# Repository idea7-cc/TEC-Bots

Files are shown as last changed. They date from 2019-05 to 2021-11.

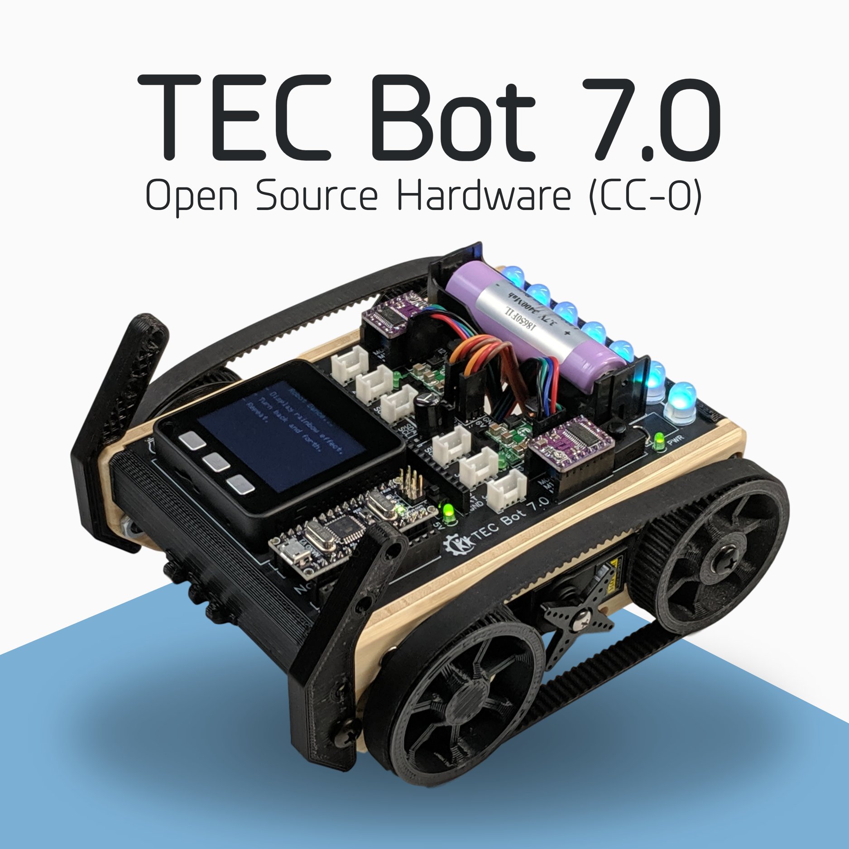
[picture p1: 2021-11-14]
TEC Bot 7/Tecbot7.jpg

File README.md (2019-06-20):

# Idea7 TEC Bots
This repo is for all of the TEC Bot series Idea7 Robots.  Robots prior to the creation of this repo may be added in time.  New TEC Bots and support files will be maintained here.

The TEC Bot series started as a spin-off of the series of robot kits that were being created by TEC Hub Foundation for Virginia Space Flight Academy's Advanced Robotics Camp.  When Cornell University added a new robotics course to their Summer College line-up, the TEC Bot series was a natural choice. 

## Robots for Cornell University's Summer College Program, "Fabricating the Future: Robotics and Programming."

- TEC Bot 3.5: 2016
- TEC Bot 4.2: 2017
- Bambot (TEC Bot 5.6): 2018
- TEC Bot 7: 2019

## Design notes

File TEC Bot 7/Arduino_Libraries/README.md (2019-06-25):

# Custom Arduino Libraries for the TEC Bot 7

- grbl4bots

# Libraries that can be found in the Arduino Library Manager

- M5Stack
- FastLED
- NewPing
- QTRSensors

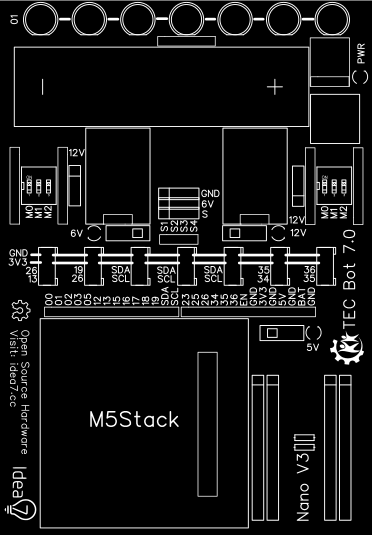
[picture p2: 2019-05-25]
TEC Bot 7/Base PCB/Top Silkscreen.png

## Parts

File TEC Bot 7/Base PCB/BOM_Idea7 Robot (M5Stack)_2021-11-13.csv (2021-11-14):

ID | Name | Designator | Footprint | Quantity | Manufacturer Part | Manufacturer | Supplier | Supplier Part | Price
1 | 1125S-4P | A1,A2,D1,D2,I2C1,I2C2,I2C3 | HW4-2.0 | 7 | 1125S-4P
2 | GPTS203211B Switch | B1 | GPTS203211B | 1 | ?
3 | BLOSSM 18650-PC2 | BAT1 | BLOSSM 18650-PC2 | 1 | BLOSSM 18650-PC2
4 | Header-Female-2.54_1x8 | DRV1,DRV2,DRV3,DRV4 | HDR-8X1/2.54 | 4 | Female headerHDR1X8-2.54 | BOOMELE | LCSC | C27438 | 0.073
5 | Header-Female-2.54_1x15 | H1,H2,H6,H7 | DIP-1X15P2.54 | 4 | 220S-1*15P H=8.5MM Ytype Gold-plated | Ckmtw | LCSC | C124408 | 0.176
6 | Header-Male-2.54_1x4 | H3,H4,H5,H8,H9 | DIP-1X4P-2.54MM-M | 5 | 210S-1*4P L=11.6MMGold-plated black | Ckmtw | LCSC | C124378 | 0.028
7 | WS2812D-F8 | LED1,LED2,LED3,LED8,LED9,LED10,LED11 | LED-8.0-RGB4P | 7 | WS2812D-F8 | Worldsemi | LCSC | C139126 | 0.161
8 | LED-3MM | LED4,LED5,LED6,LED7 | LED-3MM/2.54 | 4 | 204-10SURD/S530-A3 | EVERLIGHT | LCSC | C99772 | 0.038
9 | Header-Female-2.54_1x4 | P1,P5 | HDR-4X1/2.54 | 2 | Header-Female-2.54_1x4 | ReliaPro | LCSC | C124413 | 0.089
10 | Female header 2.54-1*14P | P2,P4 | HDR-14X1/2.54 | 2 | Female header 2.54-1*14P | BOOMELE | LCSC | C52711 | 0.075
11 | Header-Male-2.54_2x15 | P3 | HDR-15X2/2.54 | 1 | 2.54-2*15PDouble Rows | BOOMELE | LCSC | C56496 | 0.121
12 | Header-Male-2.54_1x6 | P6 | HDR-6X1/2.54 | 1 | Header-Male-2.54_1x6 | BOOMELE | LCSC | C37208 | 0.024
13 | Header-Female-2.54_1x6 | P7,S2 | HDR-6X1/2.54 | 2 | Female header 1*6p | BOOMELE | LCSC | C40877 | 0.059
14 | Header-Female-2.54_1x3 | P12,P13 | HDR-3X1/2.54 | 2 | Header2.54mm 1*3P | BOOMELE | LCSC | C49257 | 0.013
15 | 4.7K | R1,R2 | AXIAL-0.3 | 2 | ?
16 | VDG/S-03LG-R | SW1,SW5 | VDG/S-03LG-R | 2 | VDG/S-03LG-R | ReliaPro | LCSC | C52148 | 0.191
17 | EG1218 | SW2,SW3,SW4 | EG1218_1 | 3 | EG1218 | E-Switch | LCSC | C273394 | 0.766

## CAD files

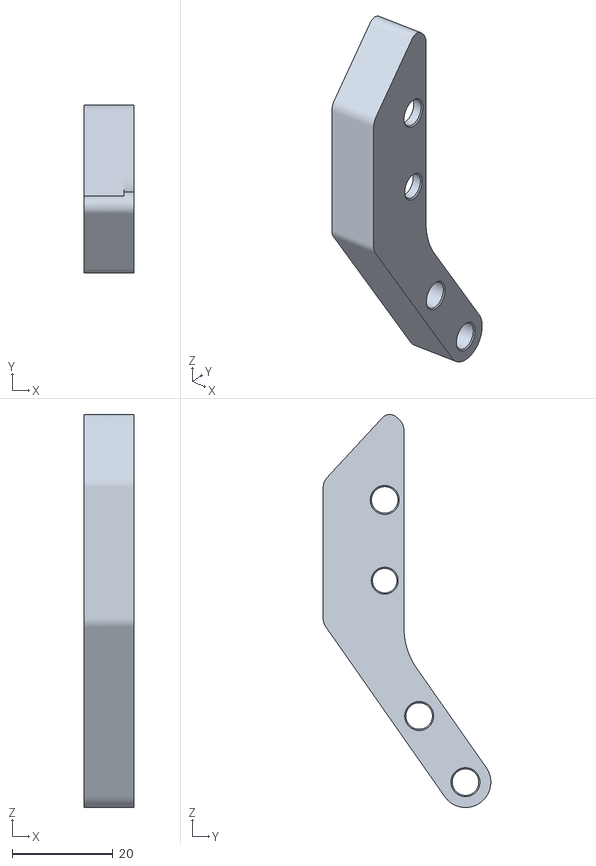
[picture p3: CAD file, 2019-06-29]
TEC Bot 7/3d Printed Parts/Balance Stand Left.stl
10.0 x 33.2 x 77.9

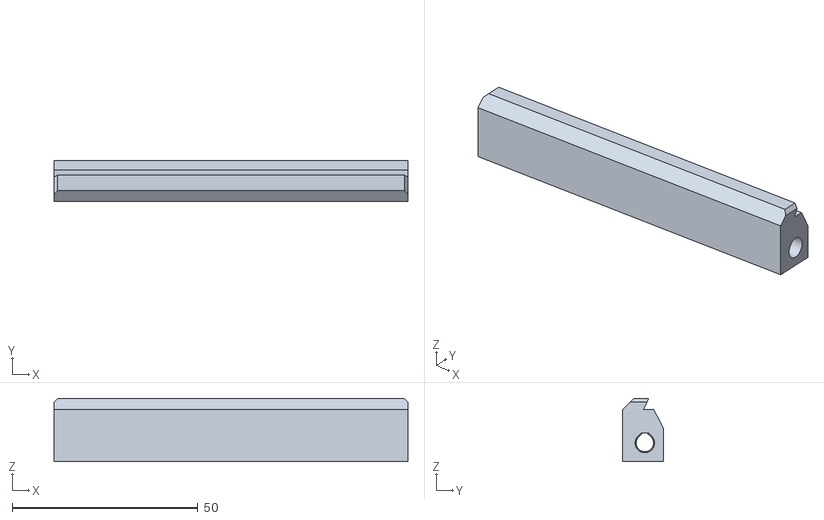
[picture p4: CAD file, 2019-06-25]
TEC Bot 7/3d Printed Parts/Cross Bar.stl
95.3 x 11.0 x 17.0

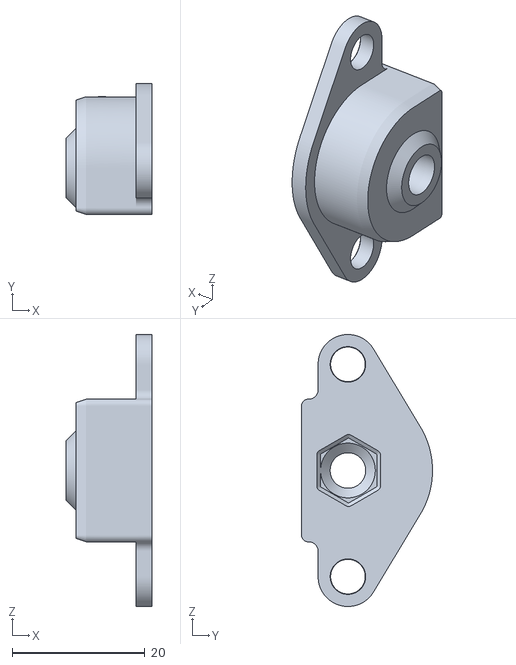
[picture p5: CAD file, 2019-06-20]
TEC Bot 7/3d Printed Parts/Idler Bracket.stl
12.9 x 19.7 x 41.0

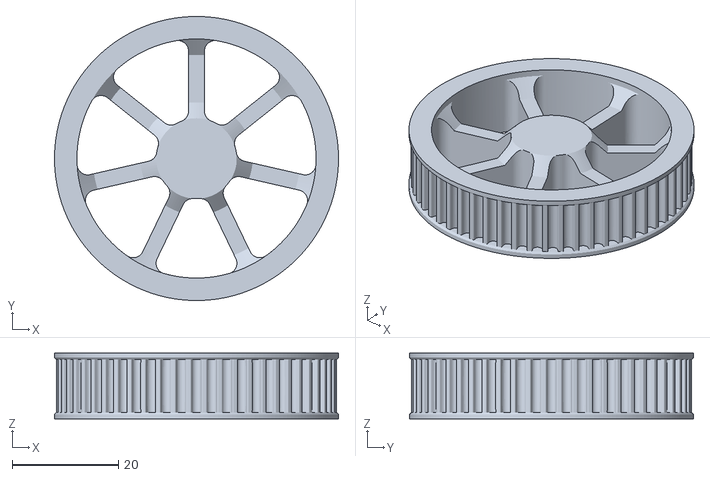
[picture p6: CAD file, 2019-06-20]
TEC Bot 7/3d Printed Parts/56 Tooth Pulley for Stepper.stl
53.5 x 53.5 x 12.4

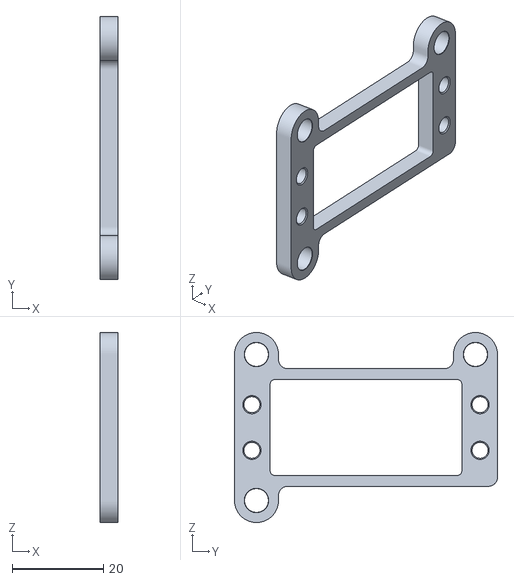
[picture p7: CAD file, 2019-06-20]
TEC Bot 7/3d Printed Parts/Servo Bracket 3 holes.stl
4.00 x 57.6 x 41.6

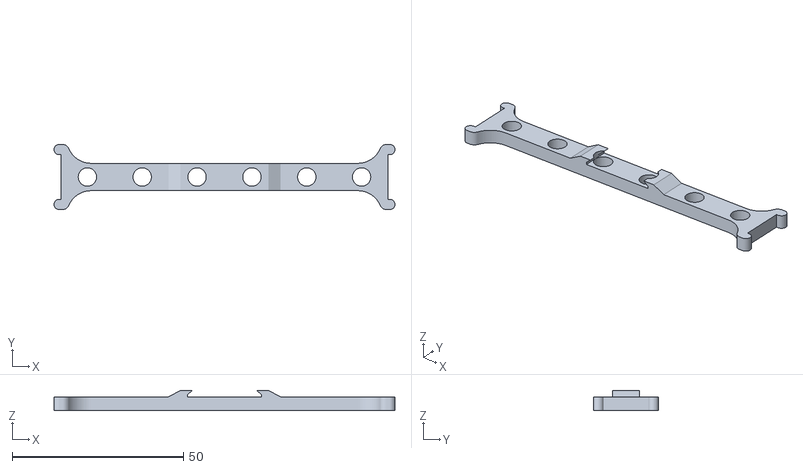
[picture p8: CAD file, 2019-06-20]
TEC Bot 7/3d Printed Parts/Accessory Bar.stl
99.5 x 19.0 x 5.90

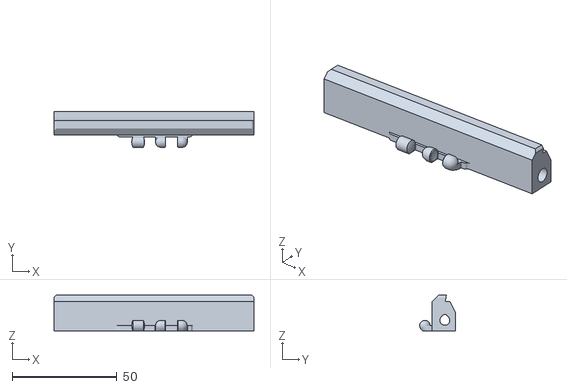
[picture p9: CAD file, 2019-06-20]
TEC Bot 7/3d Printed Parts/Polypanels Cross Bar.stl
95.3 x 17.0 x 17.0

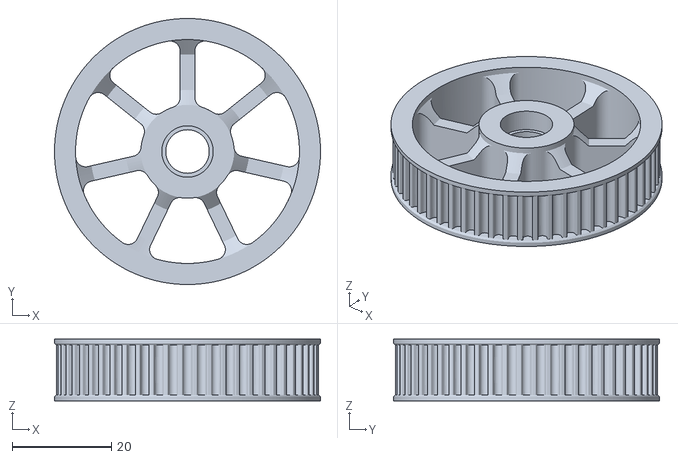
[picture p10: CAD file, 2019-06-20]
TEC Bot 7/3d Printed Parts/56 Tooth Idler.stl
53.5 x 53.5 x 12.4

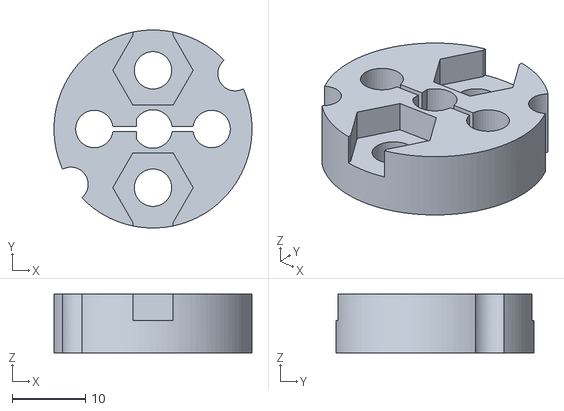
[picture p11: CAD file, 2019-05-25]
TEC Bot 7/3d Printed Parts/Stepper Wheel Hub.stl
27.0 x 27.0 x 8.00

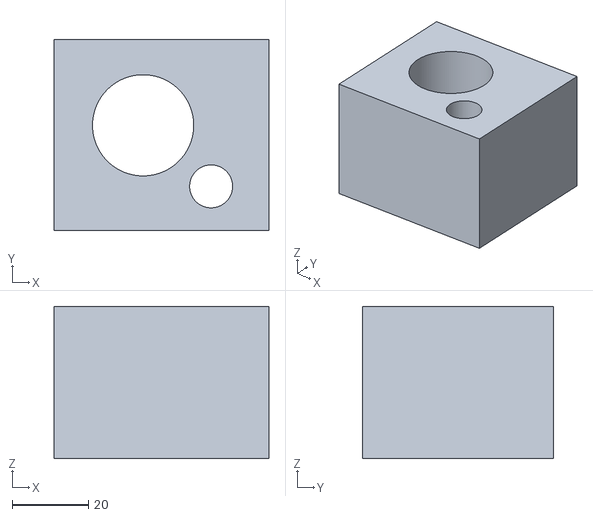
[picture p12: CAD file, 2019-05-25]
TEC Bot 7/3d Printed Parts/Body1.stl
56.4 x 50.2 x 40.0

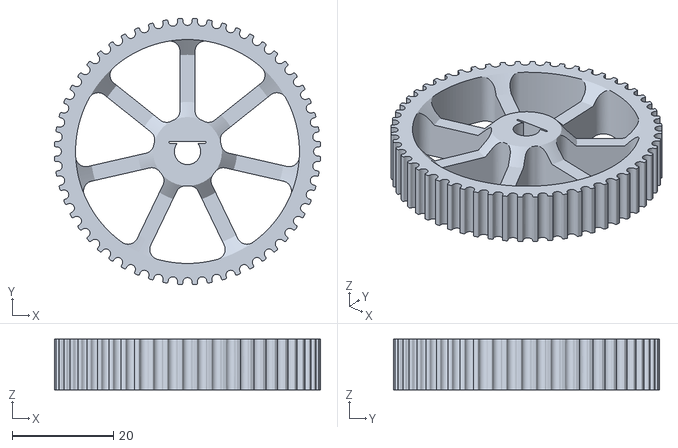
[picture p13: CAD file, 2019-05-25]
TEC Bot 7/3d Printed Parts/Belt Pully Test Profile.stl
52.7 x 52.7 x 10.0

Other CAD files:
TEC Bot 7/3d Printed Parts/Balance Stand Right.stl
TEC Bot 7/3d Printed Parts/56T Belt Pulley.stl

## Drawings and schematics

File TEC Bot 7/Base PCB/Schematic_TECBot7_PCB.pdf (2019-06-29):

# VIN VIN Header-Male⁻2.54_1x4

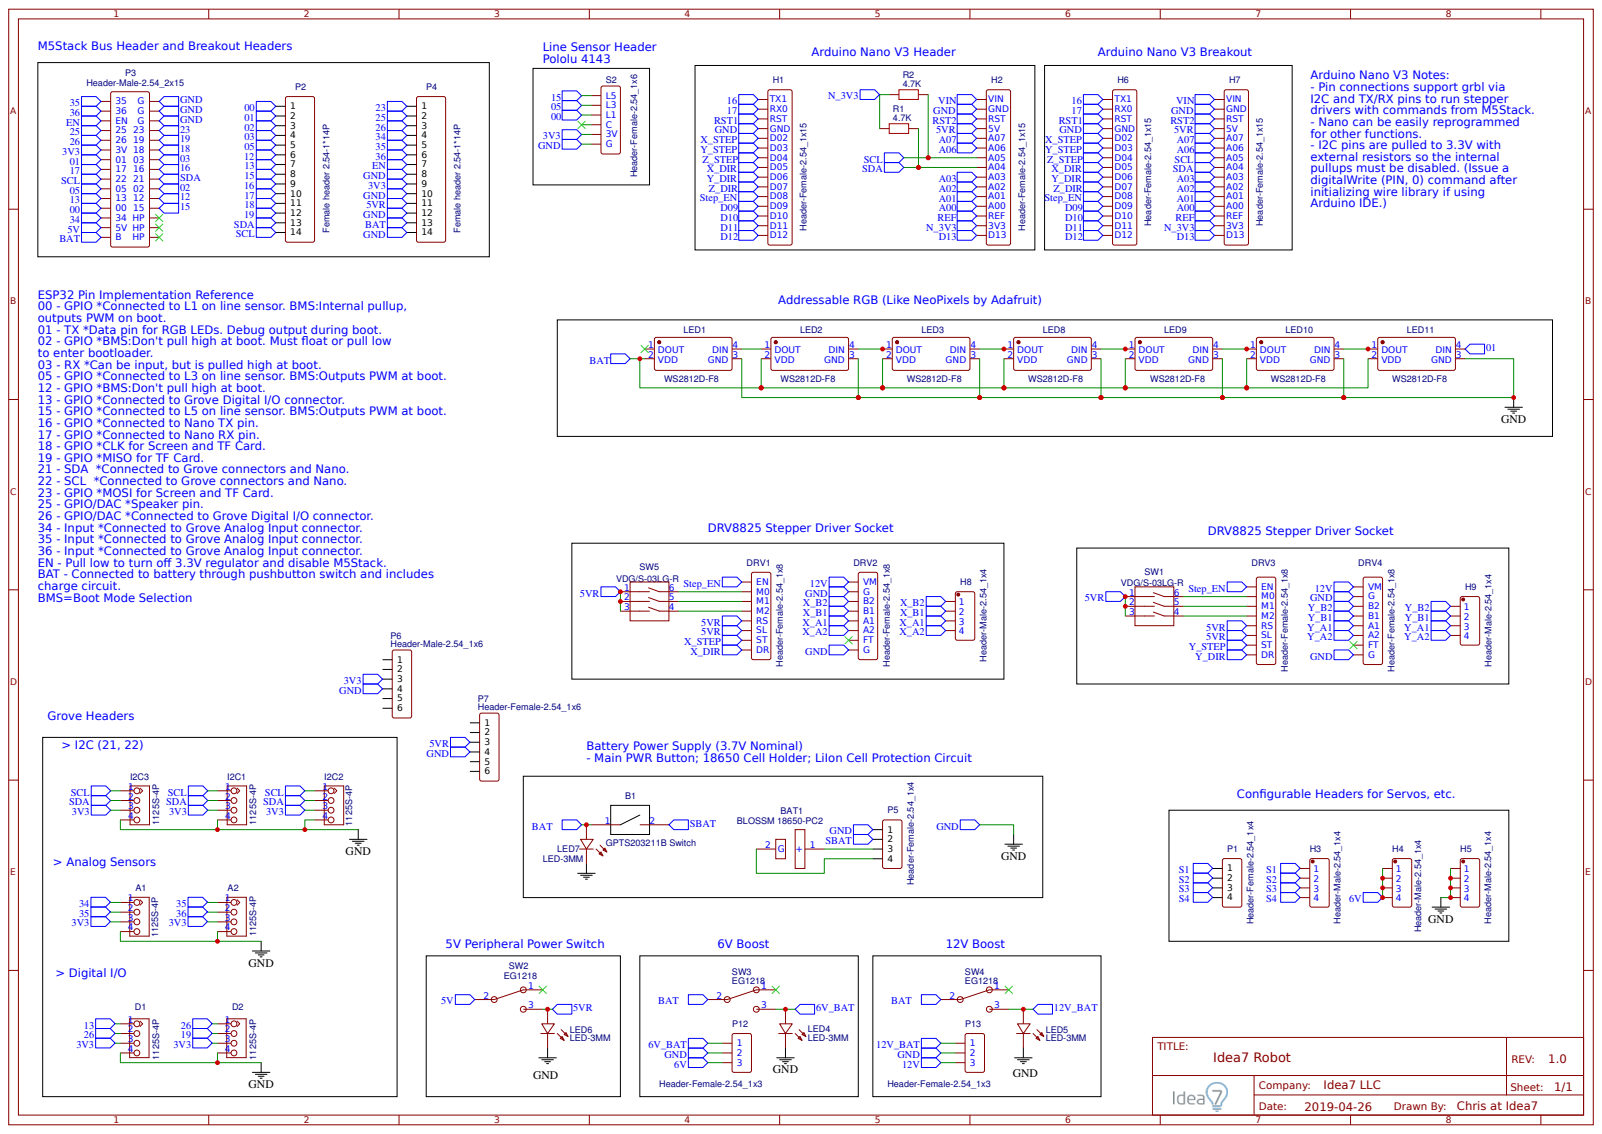
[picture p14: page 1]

M5Stack Bus Header and Breakout Headers

Arduino Nano V3 Notes:
- Pin connections support grbl via
I2C and TX/RX pins to run stepper
drivers with commands from M5Stack.
- Nano can be easily reprogrammed
for other functions.
- I2C pins are pulled to 3.3V with
external resistors so the internal

pullups must be disabled. (Issue a
digitalWrite (PIN, 0) command after
initializing wire library if using
Arduino IDE.)

ESP32 Pin Implementation Reference
00 - GPIO *Connected to L1 on line sensor. BMS:Internal pullup,
outputs PWM on boot.
01 - TX *Data pin for RGB LEDs. Debug output during boot.
02 - GPIO *BMS:Don't pull high at boot. Must float or pull low
to enter bootloader.
03 - RX *Can be input, but is pulled high at boot.
05 - GPIO *Connected to L3 on line sensor. BMS:Outputs PWM at boot.

Addressable RGB (Like NeoPixels by Adafruit)

12 - GPIO *BMS:Don't pull high at boot.
13 - GPIO *Connected to Grove Digital I/O connector.
15 - GPIO *Connected to L5 on line sensor. BMS:Outputs PWM at boot.
16 - GPIO *Connected to Nano TX pin.
17 - GPIO *Connected to Nano RX pin.
18 - GPIO *CLK for Screen and TF Card.
19 - GPIO *MISO for TF Card.
21 - SDA *Connected to Grove connectors and Nano.
22 - SCL *Connected to Grove connectors and Nano.
23 - GPIO *MOSI for Screen and TF Card.
25 - GPIO/DAC *Speaker pin.
26 - GPIO/DAC *Connected to Grove Digital I/O connector.
34 - Input *Connected to Grove Analog Input connector.
35 - Input *Connected to Grove Analog Input connector.
36 - Input *Connected to Grove Analog Input connector.
EN - Pull low to turn off 3.3V regulator and disable M5Stack.
BAT - Connected to battery through pushbutton switch and includes
charge circuit.
BMS=Boot Mode Selection

Battery Power Supply (3.7V Nominal)
- Main PWR Button; 18650 Cell Holder; LiIon Cell Protection Circuit

Configurable Headers for Servos, etc.

Drawn By: Chris at Idea7

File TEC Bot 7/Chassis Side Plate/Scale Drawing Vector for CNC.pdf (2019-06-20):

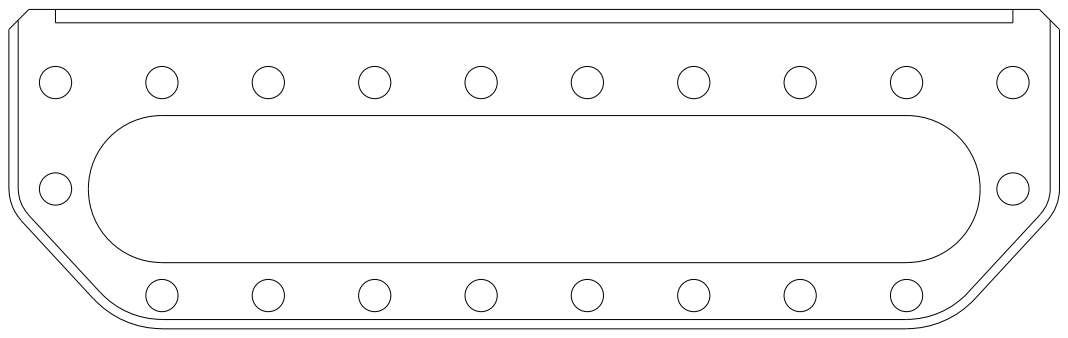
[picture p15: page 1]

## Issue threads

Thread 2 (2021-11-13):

TMC2209 driver spec

samuk, 2021-11-13:
Would you anticipate any issues with using a TMC2209 driver in place of the DRV8825? It should be quieter? https://3dwork.io/en/tmc-drivers/

chrishthompson, 2021-11-14:
Hey samuk!  I don't remember if I tried a TMC2209 driver but I probably did.  It should work.  One thing I'd consider is that quieter micro stepping modes can come with a loss of torque.

I haven't thought about this for a while, but a few things I'd recommend you consider:
- When I used an Arduino Nano clone to run GRBL, it was a workaround...it worked fine, but now that GRBL is ported to ESP-32 thanks to this project: https://github.com/bdring/Grbl_Esp32 and now this project: https://github.com/bdring/FluidNC, I think it's much better to run it directly from the M5 stack or other esp-32 board.
- I won't be much help because I'm too wrapped up in client projects these days...you might be better off with a project that has more of an active community.
- If you want to build it anyway, be ready for some of your own troubleshooting and development.
- If you do decide to build it, and you can't find a part you need, let me know.  I might have a spare.

samuk, 2021-11-14:
Thanks for the info. I did wonder about using ESP32 directly as per: https://www.tindie.com/products/33366583/tmc2209-penlaser-controller/

I'm looking to do a 100% open hardware ESP32 bot (for uROS) & I'd like to have compatibility with M5 core, so I only know of your project and https://github.com/meganetaaan/M5Mouse.

M5Mouse has a nice motor shield that fits in M5Stack, but they are using DC motors, which are hard to waterproof. My mental roadmap includes an outdoor robot and IP65 steppers are fairly available.

Some rough ideas for my project are here if you're interested: https://cloud.transition-space.org/apps/onlyoffice/s/KyTnsYjs4GRkXjZ

I'm leaning towards designing (with others) my own M5 stack 'Open Core' and 'Open Stepper driver' at the moment. But I've never designed a PCB, so expect a steep learning curve!

The nice thing about M5 is you could plug in the Odrive shield, or Canbus and start building more precise and powerful robots from the same core.

Closed 2021-11-14.

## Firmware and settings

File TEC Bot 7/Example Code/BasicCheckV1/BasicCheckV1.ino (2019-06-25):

// For TEC Bot 7.0 with grbl4bots loaded on the Nano V3 co-processor
// Grbl settings changed from default as follows
// $100=32 -- For the x axis (left motor) set to 1/16th micro stepping, this makes 100 steps equal to 1 full rotation of the wheel
// $101=32 -- Same, but for the Y axis (right motor)
// $110=63000 -- Fastest stable tested speed for 1/16th micro stepping.  Can go faster by selecting different micro stepping (hardware switch)
// $111=63000 -- Same for Y
// $120=980 -- Acceleratin that reliably prevents skipping steps
// $121=980 -- Same for Y
// 1/16th micro stepping is selected on the blue hardware switch by switching the 3rd switch on. (Off, Off, On)
// For faster speeds, you could select 1/8 microstepping (On, On, Off) but then it's possible to skip steps from too much acceleration or speed
// To use 1/8th microstepping more reliably, the config.h file in the grbl4bots library can be edited to change "DEFAULTS_TB7_16" to "DEFAULTS_TB7_8"
// For most, just stick with 1/16th microstepping!

// This program sends instructions to grbl4bots and is set with enough time between commands so that grbl doesn't get behind.
// It is also possible to send much smaller step sizes in a loop.  When grbl gets two back to back travel commands, it smoothly
// accellerates to the new command...so smooth driving can be achieved easily instead of start stop start stop.  You can use this to
// travel continuously at a constant speed.  Sending too many commands to fast can crash the buffer and cause erratic behavior.
// This will be changed in grbl4bots eventually. (Or you could fix it for us!)

// Grbl also keeps the x and y axis coordinated so they start and stop at the same time.  This makes it easy to do smooth turns for example.

// The FastLED library is used instead of the Neopixel library because the Neopixel library conflicts with the m5Stack library somehow

// This example makes the robot turn back and forth.

#include <M5Stack.h>
#include "FastLED.h"

#define Neopixel_PIN 1
#define NUM_LEDS 7

CRGB leds[NUM_LEDS];
uint8_t gHue = 0;
static TaskHandle_t FastLEDshowTaskHandle = 0;
static TaskHandle_t userTaskHandle = 0;

int forwardSpeed = 21000; //medium
int backSpeed = 21000; //medium
int driveDistance = 0; //positive numbers are FWD. 100 = 1 full revolution
int driveRotation = 21;  //positive numbers are CW
unsigned long timeOfLastTurn = 0;
int timeSinceLastTurn = 0;
int turnInterval = 310;

void setup() 
{
  M5.begin();
  M5.Lcd.clear(BLACK);
  M5.Lcd.setTextColor(CYAN); M5.Lcd.setTextSize(2); M5.Lcd.setCursor(40, 0);
  M5.Lcd.println("Robot Dance...");
  M5.Lcd.setTextColor(WHITE);
  M5.Lcd.setCursor(0, 25);
  M5.Lcd.println();
  M5.Lcd.println("- Display rainbow effect.");
  M5.Lcd.println();
  M5.Lcd.println("- Turn back and forth.");
  M5.Lcd.println();
  M5.Lcd.println("- Repeat.");

  // Neopixel initialization
  FastLED.addLeds<WS2811,Neopixel_PIN,GRB>(leds, NUM_LEDS).setCorrection(TypicalLEDStrip);
  FastLED.setBrightness(10);
  xTaskCreatePinnedToCore(FastLEDshowTask, "FastLEDshowTask", 2048, NULL, 2, NULL, 1);

  // Serial2.begin(unsigned long baud, uint32_t config, int8_t rxPin, int8_t txPin, bool invert)
  Serial2.begin(115200, SERIAL_8N1, 16, 17);
  
  //give grbl time to start up on Nano
  delay(4000); 
}

void loop() 
{
  timeSinceLastTurn=millis()-timeOfLastTurn; //calculate time since last turn (or time since start)

  if(timeSinceLastTurn>turnInterval) //if it's time to turn again
  {
    Serial2.print("\r\n\r\n"); //wakes up grbl
    delay(2);
    Serial2.print("$J=G21G91X");  //send move command to grbl
    Serial2.print(driveDistance+driveRotation);  //move left motor this far
    Serial2.print("Y");
    Serial2.print(driveDistance-driveRotation);  //move right motor this far
    Serial2.print("F");
    Serial2.print(forwardSpeed);  //move this fast (acceleration is automatically handled by grbl)
    driveRotation=-driveRotation;  //flip the direction
    timeOfLastTurn=millis();    //capture the time we did this turn so we can decide when to do the next one
  }
}  

void FastLEDshowESP32()
{
    if (userTaskHandle == 0) {
        userTaskHandle = xTaskGetCurrentTaskHandle();
        xTaskNotifyGive(FastLEDshowTaskHandle);
        const TickType_t xMaxBlockTime = pdMS_TO_TICKS( 200 );
        ulTaskNotifyTake(pdTRUE, xMaxBlockTime);
        userTaskHandle = 0;
    }
}

void FastLEDshowTask(void *pvParameters)
{
    for(;;) {
        fill_rainbow(leds, NUM_LEDS, gHue, 7);// rainbow effect
        FastLED.show();// must be executed for neopixel becoming effective
        EVERY_N_MILLISECONDS( 20 ) { gHue++; }
    }
}

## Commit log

2019-05-25 Added TEC Bot 7
    [56T Belt Pulley.stl, Belt Pully Test Profile.stl, Body1.stl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]
2019-05-25 Create Top Silkscreen.png
2019-06-20 Adding serveral files
    [56 Tooth Idler.stl, 56 Tooth Pulley for Stepper.stl, Accessory Bar.stl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]
2019-06-21 Added Colorful Back-N-Dash example
    Needs ESP32, M5Stack, and FastLED Libraries. Needs grbl installed on Nano and configured. 1/16th micorstepping. Demonstrates mostly non-blocking code. Robot backs up and then dashes forward an equal 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
2019-06-21 minor tweak to Pulley factory, added notes to example program
2019-06-25 Added grbl with minor changes and other tweaks
    [Cross Bar.stl, config.h, cpu_map.h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]
2019-06-25 added a library folder for custom libs
    [config.h, cpu_map.h, defaults.h]
2019-06-29 Added schematic for pcb
2019-06-29 Added updated 3dprint files
    [Balance Stand Left.stl, Balance Stand Right.stl]
2021-11-13 Added the Gerbers & BOM
    Grabbed from https://easyeda.com/editor#id=27758ebc00cf4b5ca4d2bfc906883be5|94f1eed99ac44db8861310acc40319bf
    [BOM_Idea7 Robot (M5Stack)_2021-11-13.csv]
